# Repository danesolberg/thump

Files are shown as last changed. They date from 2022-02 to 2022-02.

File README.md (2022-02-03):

# thump
An automatic ceiling thumper for noisy neighbors using a piezo vibration sensor and pneumatics.

Because nobody has time for broom handles.

## Prototype


## Features
- Runs on Arduino microcontrollers
- Monitors neighbors' stomping and triggers a thump based on a configurable stomp threshold
- Accepts IR remote signal to change thump threshold, manually trigger thumps, or arm/disarm
- Uses standard 3000psi air tanks
- **Full-auto thumping**

## Schematic / Components
(schematic and component list to be added)
- Accepts an analog output voltage (PWM from 0V to 5V) from a microcontroller, combined with a low-pass filter for smoothing, to set a reference voltage that acts as a threshold for activating the thump
- Detects ceiling vibration using a piezoelectric sensor, which converts vibration to a high-voltage, low current signal.  Normalizes this voltage then amplifies the signal using one comparator in the LM358 op-amp
- Uses the second comparator in the op-amp to compare the vibration signal voltage to the threshold voltage from the Arduino, activating a transistor that powers a pneumatic solenoid when a thump is required

Breadboard

## Video Example
https://user-images.githubusercontent.com/25882507/152405606-cf46f67b-545c-4870-9b66-d56ac1f80335.MOV

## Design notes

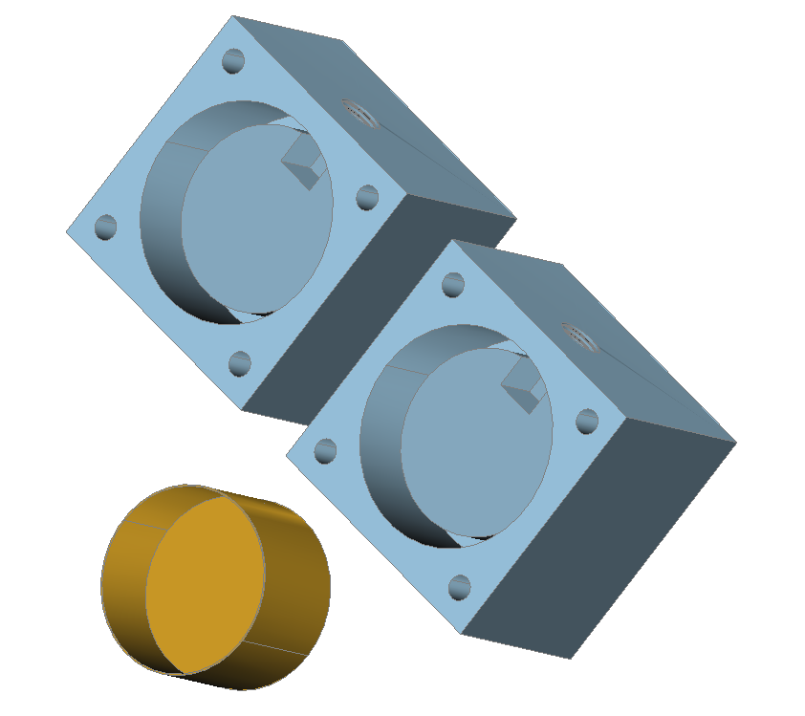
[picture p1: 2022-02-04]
end-caps-cad-screenshot.png

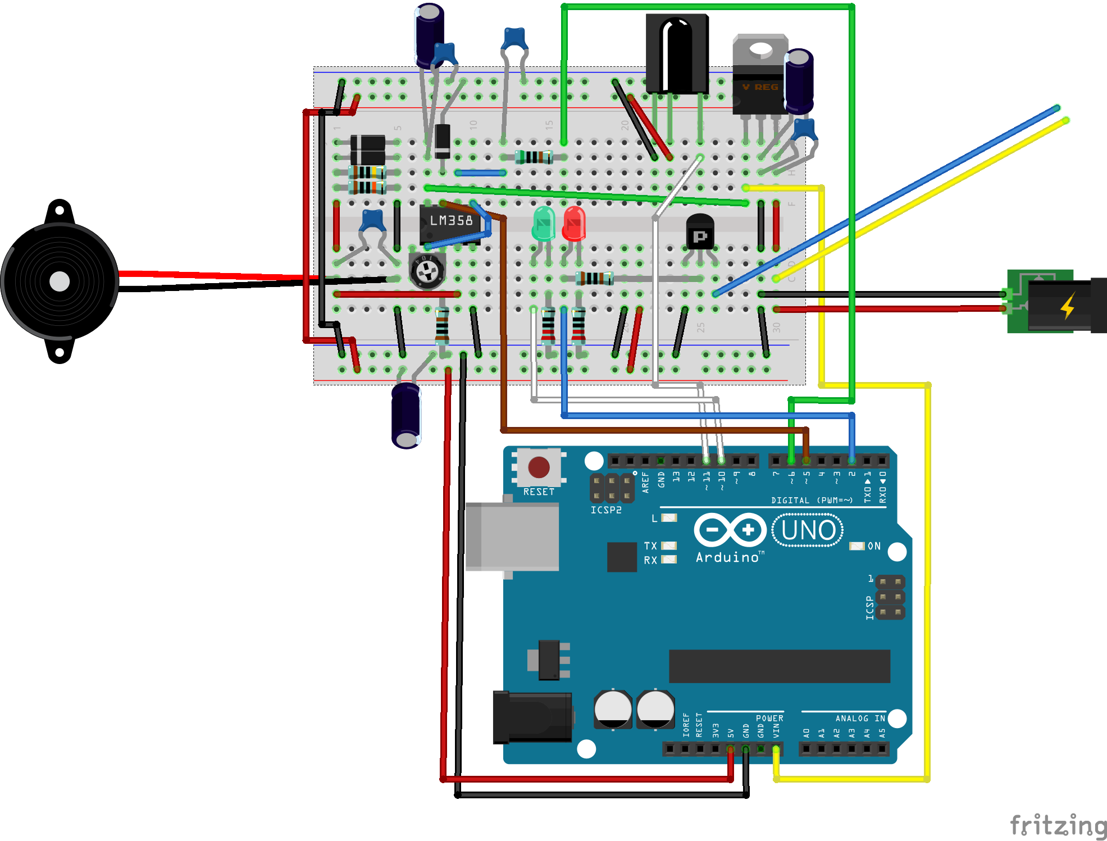
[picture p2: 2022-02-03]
thumper_bb.png

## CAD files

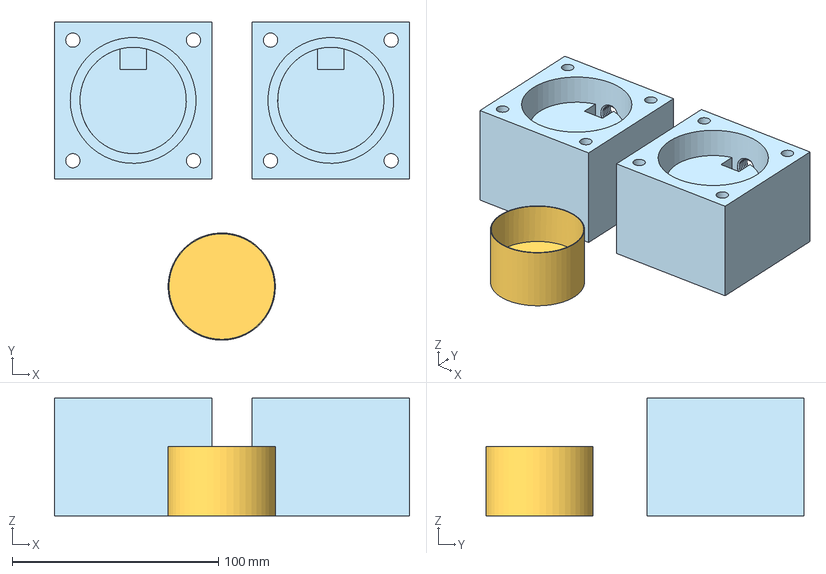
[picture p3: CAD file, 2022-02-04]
Thumper_3D_Printed_Parts.step
172.0 x 154.3 x 57.2 mm

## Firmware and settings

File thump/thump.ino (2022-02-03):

#include "IRremote.h"
#include "IR.h"
#include <EEPROM.h>

#define VIBRATION_DIGITAL_IN_PIN 5
#define SOLENOID_DIGITAL_OUT 2
#define THRESHOLD_PWM_OUT_PIN 6
#define IR_RECEIVER_IN_PIN 11
#define ARMED_STATUS_OUT_PIN 10

IRrecv irrecv(IR_RECEIVER_IN_PIN);     // create instance of 'irrecv'
decode_results results;      // create instance of 'decode_results'

// core values for thump function
const int DEBOUNCE = 250; // milliseconds to not trigger again
int holdOpen = 100; // ms to hold open solenoid
unsigned long lastThump;
bool updatingHoldOpen = false; // logical flag for interval to change hold open on remote
unsigned long updatingHoldOpenSince; // timestamp for start of hold open update interval
int holdOpenBuffer [3] = {0, 0, 0}; // array to hold new hold open value
unsigned int holdOpenBufferLength = 0; // current length of holdOpenBuffer
const int EE_HOLD_OPEN_ADDRESS = 1;  // storage address for holdOpen

// remote constants
const float REMOTE_NUM_MAX = 9.0; // max numeric on remote
const int REMOTE_INTERVAL = 3000; // ms to record remote activity

// values to maintain thump threshold
int pwmValue; // PWM value fed into low-pass RC filter for 0-5V output for op-amp comparator
const int EE_THRESHOLD_ADDRESS = 0;  // storage address for pwmValue
const int THRESHOLD_DELTA = 1; // interval to change theshold each inc/dec
bool updatingThreshold = false; // logical flag for interval to change threshold on remote
unsigned long updatingThresholdSince; // timestamp for start of threshold update interval

// arming values
bool armedStatus = false; // logical flag for armed status
bool armedSignal = false; // maintain output signal to armed status LED
const int ARMED_SIGNAL_LEVEL = 100; // PWM value to light armed status LED
unsigned long previousMillis = 0; 


void setup() {
  pinMode(VIBRATION_DIGITAL_IN_PIN, INPUT);
  pinMode(SOLENOID_DIGITAL_OUT, OUTPUT);
  pinMode(THRESHOLD_PWM_OUT_PIN, OUTPUT);
  pinMode(ARMED_STATUS_OUT_PIN, OUTPUT);
  analogWrite(THRESHOLD_PWM_OUT_PIN, pwmValue);
  lastThump = millis();
  lookupStoredLevels();
  irrecv.enableIRIn();
}

void lookupStoredLevels() {
  pwmValue = EEPROM.read(EE_THRESHOLD_ADDRESS);
  analogWrite(THRESHOLD_PWM_OUT_PIN, pwmValue);
  holdOpen = EEPROM.read(EE_HOLD_OPEN_ADDRESS);
}

void triggerThump() {
  digitalWrite(SOLENOID_DIGITAL_OUT, HIGH);
  lastThump = millis();
}

void resetThump() {
  digitalWrite(SOLENOID_DIGITAL_OUT, LOW);
}

void incrementThreshold() {
  pwmValue = min(255, pwmValue + THRESHOLD_DELTA);
  analogWrite(THRESHOLD_PWM_OUT_PIN, pwmValue);
  EEPROM.write(EE_THRESHOLD_ADDRESS, pwmValue);
}

void decrementThreshold() {
  pwmValue = max(0, pwmValue - THRESHOLD_DELTA);
  analogWrite(THRESHOLD_PWM_OUT_PIN, pwmValue);
  EEPROM.write(EE_THRESHOLD_ADDRESS, pwmValue);
}

void jumpThreshold(int value) {
  pwmValue = round((value / REMOTE_NUM_MAX) * 255);
  analogWrite(THRESHOLD_PWM_OUT_PIN, pwmValue);
  EEPROM.write(EE_THRESHOLD_ADDRESS, pwmValue);
}

void flipArmedStatus() {
  armedStatus = !armedStatus;
}

void closeThresholdUpdateInterval() {
  updatingThreshold = false;
  updatingThresholdSince = 0;
}

void closeHoldOpenUpdateInterval() {
    updatingHoldOpen = false;
    updatingHoldOpenSince = 0;
    // convert array of digits into applicable integer; [1,2,3] == 123
    if (holdOpenBufferLength > 0) {
      int num = 0;
      int place = 1;
      for (int i = holdOpenBufferLength-1; i >= 0; i--) {
        num += holdOpenBuffer[i] * place;
        place *= 10;
      }
      holdOpen = num;
      EEPROM.write(EE_HOLD_OPEN_ADDRESS, holdOpen);
    }
}

void blinkStatusLight() {
  unsigned long currentMillis = millis();
  
  if (currentMillis - previousMillis >= 100) {
    previousMillis = currentMillis;
    armedSignal = !armedSignal;
    analogWrite(ARMED_STATUS_OUT_PIN, ARMED_SIGNAL_LEVEL * armedSignal);
  }
}

void receiveIR() {
  int tmpValue;
  
  if (irrecv.decode(&results)) // have we received an IR signal?
  {
    for (int i = 0; i < 23; i++)
    {
      if ((i<KEY_NUM) && (keyValue[i] == results.value))
      {
        tmpValue = results.value;

        if (results.value == KEY_VOL_ADD) {
          incrementThreshold();
        } else if (results.value == KEY_VOL_DE) {
          decrementThreshold();
        } else if (results.value == KEY_PAUSE) {
          triggerThump();
        } else if (results.value == KEY_POWER) {
          flipArmedStatus();
        } else if (results.value == KEY_FUNC_STOP) {
          // begin time interval wherein the thump vibration trigger threshold can be set
          closeHoldOpenUpdateInterval();
          updatingThreshold = true;
          updatingThresholdSince = millis();
        } else if (updatingThreshold == true && 0 <= keyBuf[i] <= 9) {
          jumpThreshold(atoi(keyBuf[i]));
        } else if (results.value == KEY_ST_REPT) {
          // close time interbal wherein the thump vibration trigger threshold can be set
          closeThresholdUpdateInterval();
          updatingHoldOpen = true;
          updatingHoldOpenSince = millis();
          for (int i = 0; i < 3; i++) {
            holdOpenBuffer[i] = 0;
          }
          holdOpenBufferLength = 0;
        } else if (updatingHoldOpen == true && holdOpenBufferLength < 3 && 0 <= keyBuf[i] <= 9) {
          // append digit of key to the current thump vibration trigger threshold value
          holdOpenBuffer[holdOpenBufferLength++] = atoi(keyBuf[i]);
        }
      }
      else if(VAL_REPEAT==i)
      {
        results.value = tmpValue;
      }
    }
    irrecv.resume(); // receive the next value
  }
}

void loop() {
  if (armedStatus == true && digitalRead(VIBRATION_DIGITAL_IN_PIN) == HIGH && millis() > lastThump + DEBOUNCE) {
    triggerThump();
  }

  if (digitalRead(SOLENOID_DIGITAL_OUT) == HIGH && millis() > lastThump + holdOpen) {
    resetThump();
  }
  
  receiveIR();

  if (updatingThreshold == true || updatingHoldOpen == true) {
    blinkStatusLight();

    if (updatingThreshold == true && millis() > updatingThresholdSince + REMOTE_INTERVAL) {
      closeThresholdUpdateInterval();
    } else if (updatingHoldOpen == true && millis() > updatingHoldOpenSince + REMOTE_INTERVAL) {
      closeHoldOpenUpdateInterval();
    }
  } else {
    if (armedStatus == true && armedSignal == false) {
      analogWrite(ARMED_STATUS_OUT_PIN, ARMED_SIGNAL_LEVEL);
      armedSignal = true;
    } else if (armedStatus == false && armedSignal == true) {
      analogWrite(ARMED_STATUS_OUT_PIN, 0);
      armedSignal = false;
    }
  }
}
